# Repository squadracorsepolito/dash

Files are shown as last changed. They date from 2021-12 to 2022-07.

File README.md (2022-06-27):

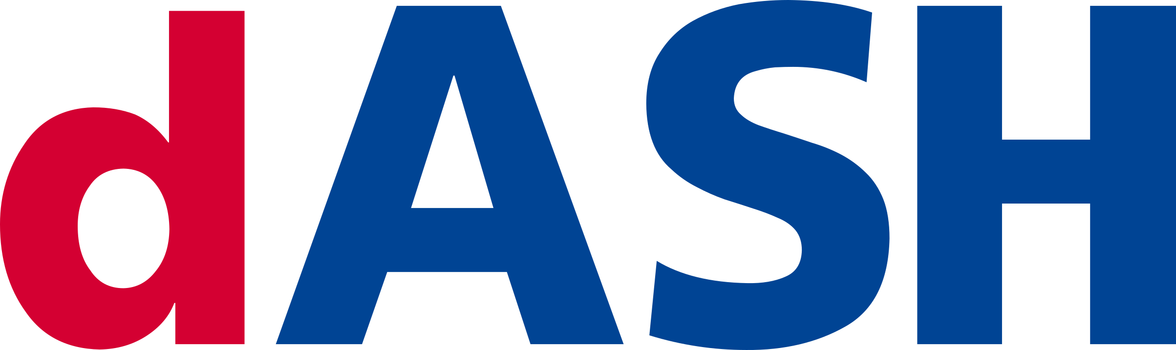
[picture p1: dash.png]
Dash

Benvenuti nella repository ufficiale certificata contenente i file utilizzati per la scheda NuovaDash22© utilizzata dal team Squadra Corse Driverless nell'anno 2021/22

Repository mantenuta da Matteo Bonora (Software) e Francesco Minichelli (Hardware e Software)

## How to use the makefile
This project is generated to work with bare makefiles instead of the STM32CubeIDE. In order to successfully use the makefiles, you need to have a few tools installed. Refer to [this](https://www.bonnee.me/blog/stm32-vscode/) guide on how to setup your environment and install the needed tools (Visual Studio Code is optional and only needed to do debugging and to regenerate the makefile after regenerating code through STM32CubeMX).

If you want to **flash over CAN-bus**, you will need an [additional tool](https://github.com/arkku/srec) to convert the `.bin` firmware file to `.srec` and [bootcommander](https://www.feaser.com/openblt/doku.php?id=manual:bootcommander) to send the firmware to the dashboard.

### Build
In order to build the project, issue the following command:
`make -f STM32Make.make`
You can call `make clean` to clean the build directory.

### Flash
To configure the `can0` interface on your computer, you can call `make can` with root privileges.

`make canflash` will automatically convert the firmware to Motorola S-Record and pass it to bootcommander. If you only want to have the `.srec` file, you can call `make srec`

## Configurazione STM32CubeIDE per upload software tramite CAN

Project Properties -> C/C++ Build -> Settings -> Tool Settings -> MCU Post build outputs -> Selezionare "Convert to Motorola S-record file (-O ihex)"

### Run this command on the terminal to upload the code

1) Setup CAN0 interface with a Kvaser device connected to the PC Host
2a) Open MicroBoot
2b) Open BootCommander (same as MicroBoot but on a terminal)
3) Make sure the Target board is off and the can bus of the board connected to the Kvaser
  - There should be no problem if other device are connected on same can bus. If problem arises, turn off all other devices.
4a) Setup MicroBoot with the firmware to upload. 
4b) Lunch the terminal command
5) Power on the Target board.

```shell
cd /home/francesco/Desktop/openblt-master/Host
sudo ip link set can0 type can bitrate 1000000
sudo ip link set can0 up
./MicroBoot
```

La configurazione attuale è la seguente
CAN SPEED = 1Mbit
CAN message ID target-\>host = (0xFFA)
CAN message ID host-\>target = (0x007)

## Analisi NuovaDash22

I Micro attualmente utilizzati sono:
- STM32F303VCTx (256Kb version)
- STM32F303VETx (512Kb version)

Le periferiche attualmente utilizzate sono:
- CAN
- GPIO

Di seguito una descrizione (tensione, impedenza) per ogni pin del connettore in base all'uscita del micro.

| Signal Name  	| GPIO PIN SET 	 | GPIO PIN RESET | PIN NAME |
| --- | --- | --- | --- |
| ASB CMD  	| ASB LED ON  	 | ASB LED OFF	  | PA8 |
| AMS CMD  	| AMS LED ON  	 | AMS LED OFF | PC6 |
| IMD CMD  	| IMD LED ON  	 | IMD LED OFF | PC8 |
| RTD CMD  	| RTD LED ON  	 | RTD LED OFF | PC6 |
| TSOFF CMD  	| TSOFF LED ON 	 | TSOFF LED OFF  | PC11 |
| ASSI B CMD  	| ASSI B LED OFF | ASSI B LED ON  | PB8 |
| ASSI Y CMD  	| ASSI Y LED OFF | ASSI Y LED ON  | PB7 |
| AMI 1 CMD  	| AMI 1 LED OFF  | AMI 1 LED ON | PB5 |
| AMI 2 CMD  	| AMI 2 LED OFF  | AMI 2 LED ON | PD6 |
| AMI 3 CMD  	| AMI 3 LED OFF  | AMI 3 LED ON | PD4 |

Appena la scheda parte, sia durante il bootloader che durante le prime fasi del programma (1 secondo di bootloader + [0-2.5 max] secondi di programma), al fine di rispettare la regola T11.9.5 che cito: 

> T 11.9.5 Indicators according to T 11.9.1 with safe state “illuminated” (e.g. absence of failures is not actively indicated) must be illuminated for 1 s to 3 s for visible check after power cycling the LVMS. 

ci si aspetta il seguente stato per ogni apparato della macchina:

- LED ASSI YELLOW (durante i test questo colore sarà BLU)
- LED AMI tutti accesi
- BuzzerAS Spento
- BuzzerEv Spento
- Cockpit tutto acceso tranne TSOFF

### Analisi Dashboard SC19

La scheda può essere suddivisa in 4 sezioni:

- MCU (STM32)
- Input/Output (Connettore)
- Alimentazione (DC/DC)
- Condizionamento Output/Input

### MCU (STM32)
Il micro utilizzato è un **STM32F303VCT**. 
- Alimentato con una tensione di 3.3V (ricavata tramite modulo DC/DC sulla scheda)
- Collegamento CAN con transreceiver SN65HVD234
- Connettore SWD
- Tre LED sulla scheda, RED/GREEN/BLUE, collegati rispettivamente ai pin PE11, PE12, PA3 e comandati tramite MOSFET (sulla scheda)
- GPIO (verranno spiegati in seguito)
  - PD10 : Imd\_Err\_Led\_Cmd
  - PE2: Buzzer\_CMD
  - PE3: No\_Hv\_Led\_CMD
  - PE5: Rtd\_Led\_CMD
  - PD13: PWM1
  - PD14: PWM2
  - PD15: PWM3
  - PA1: spare\_button
  - PA2: RTD\_button (RTD\_In)
  - PB9: BMS\_Led\_Cmd
- I2C
- USART
### Input/Output (Connettore)
### Alimentazione (DC/DC)
Input a 24V e output a 5V e 3.3V. Per la 5V è stato utilizzato un LMZ14202TZE e per la 3.3V un LM1117-3.3
### Condizionamento Output/Input
I seguenti segnali, provenienti dal connettore, sono collegati a un MOSFET con Source collegato a massa. Tra parentesi, il nome del GPIO della STM che controlla il mosfet
- IMD\_LED (IMD\_LED\_CMD)
- BMS\_LED (BMS\_LED\_CMD)
- RTD\_LED (RTD\_LED\_CMD)
- BUZZER (BUZZER\_CMD)
- No\_Hv\_Led (No\_Hv\_Led\_CMD)
- PUMP\_AUTO (PWM3)
- BP\_FAN\_AUTO (PWM2)
- RAD\_FAN\_AUTO (PWM1)

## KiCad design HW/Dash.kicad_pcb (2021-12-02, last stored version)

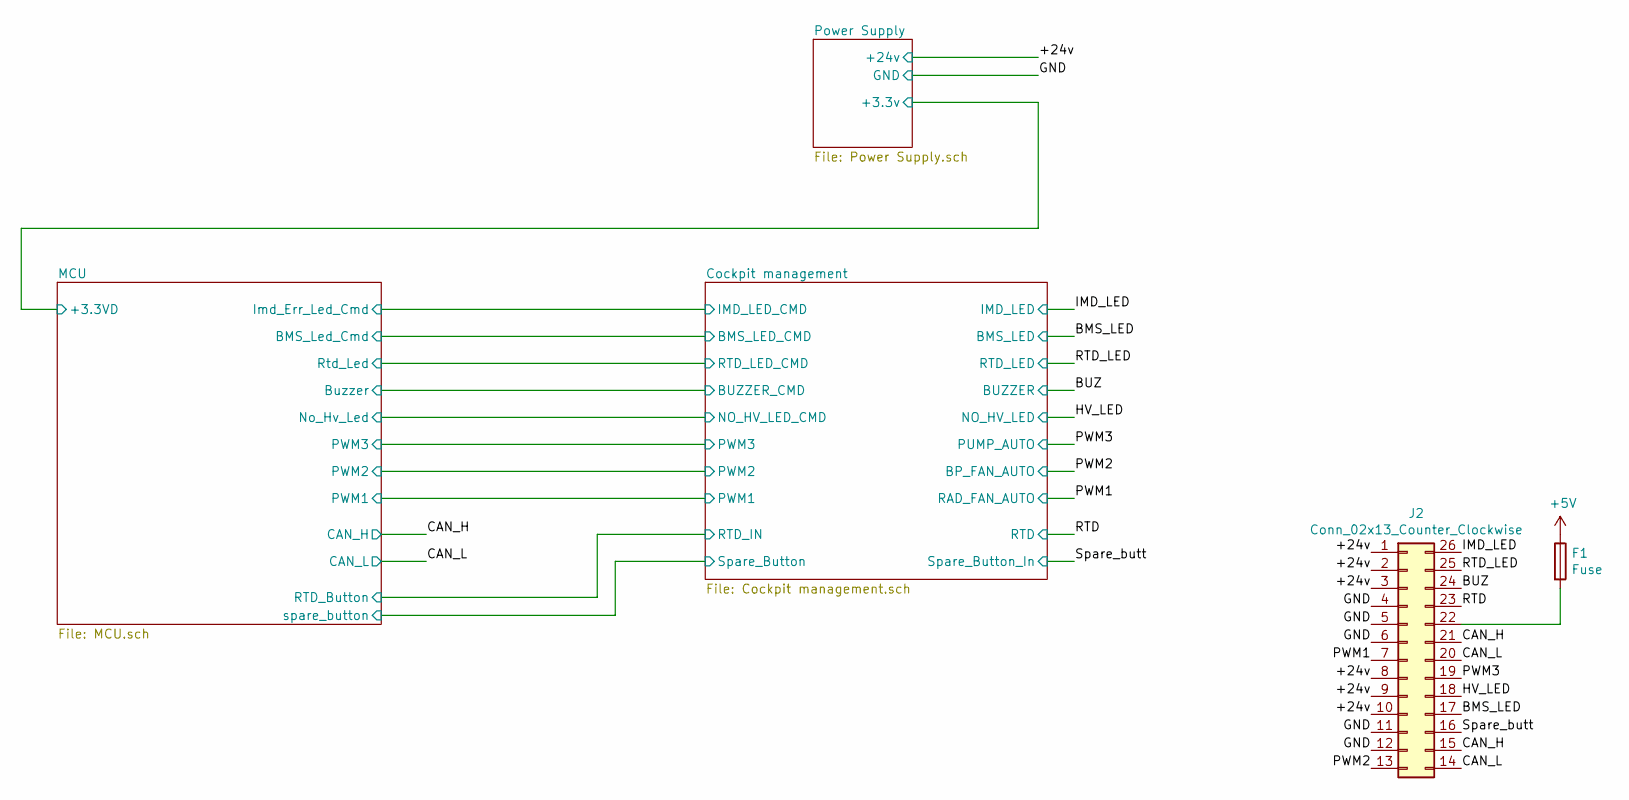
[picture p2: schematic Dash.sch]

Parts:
F1: Fuse; Fuse_0805_2012Metric_Pad1.15x1.40mm_HandSolder
J2: Conn_02x13_Counter_Clockwise; TE_9-6437287-8

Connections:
+5V: F1.1; also elsewhere on the board
/+24v: J2.1, J2.2, J2.3, J2.8, J2.9, J2.10; also elsewhere on the board
/BMS_LED: J2.17; also elsewhere on the board
/BUZ: J2.24; also elsewhere on the board
/CAN_H: J2.15, J2.21; also elsewhere on the board
/CAN_L: J2.14, J2.20; also elsewhere on the board
/HV_LED: J2.18; also elsewhere on the board
/IMD_LED: J2.26; also elsewhere on the board
/PWM1: J2.7; also elsewhere on the board
/PWM2: J2.13; also elsewhere on the board
/PWM3: J2.19; also elsewhere on the board
/RTD: J2.23; also elsewhere on the board
/RTD_LED: J2.25; also elsewhere on the board
/Spare_butt: J2.16; also elsewhere on the board
GND: J2.4, J2.5, J2.6, J2.11, J2.12; also elsewhere on the board
unnamed: F1.2, J2.22

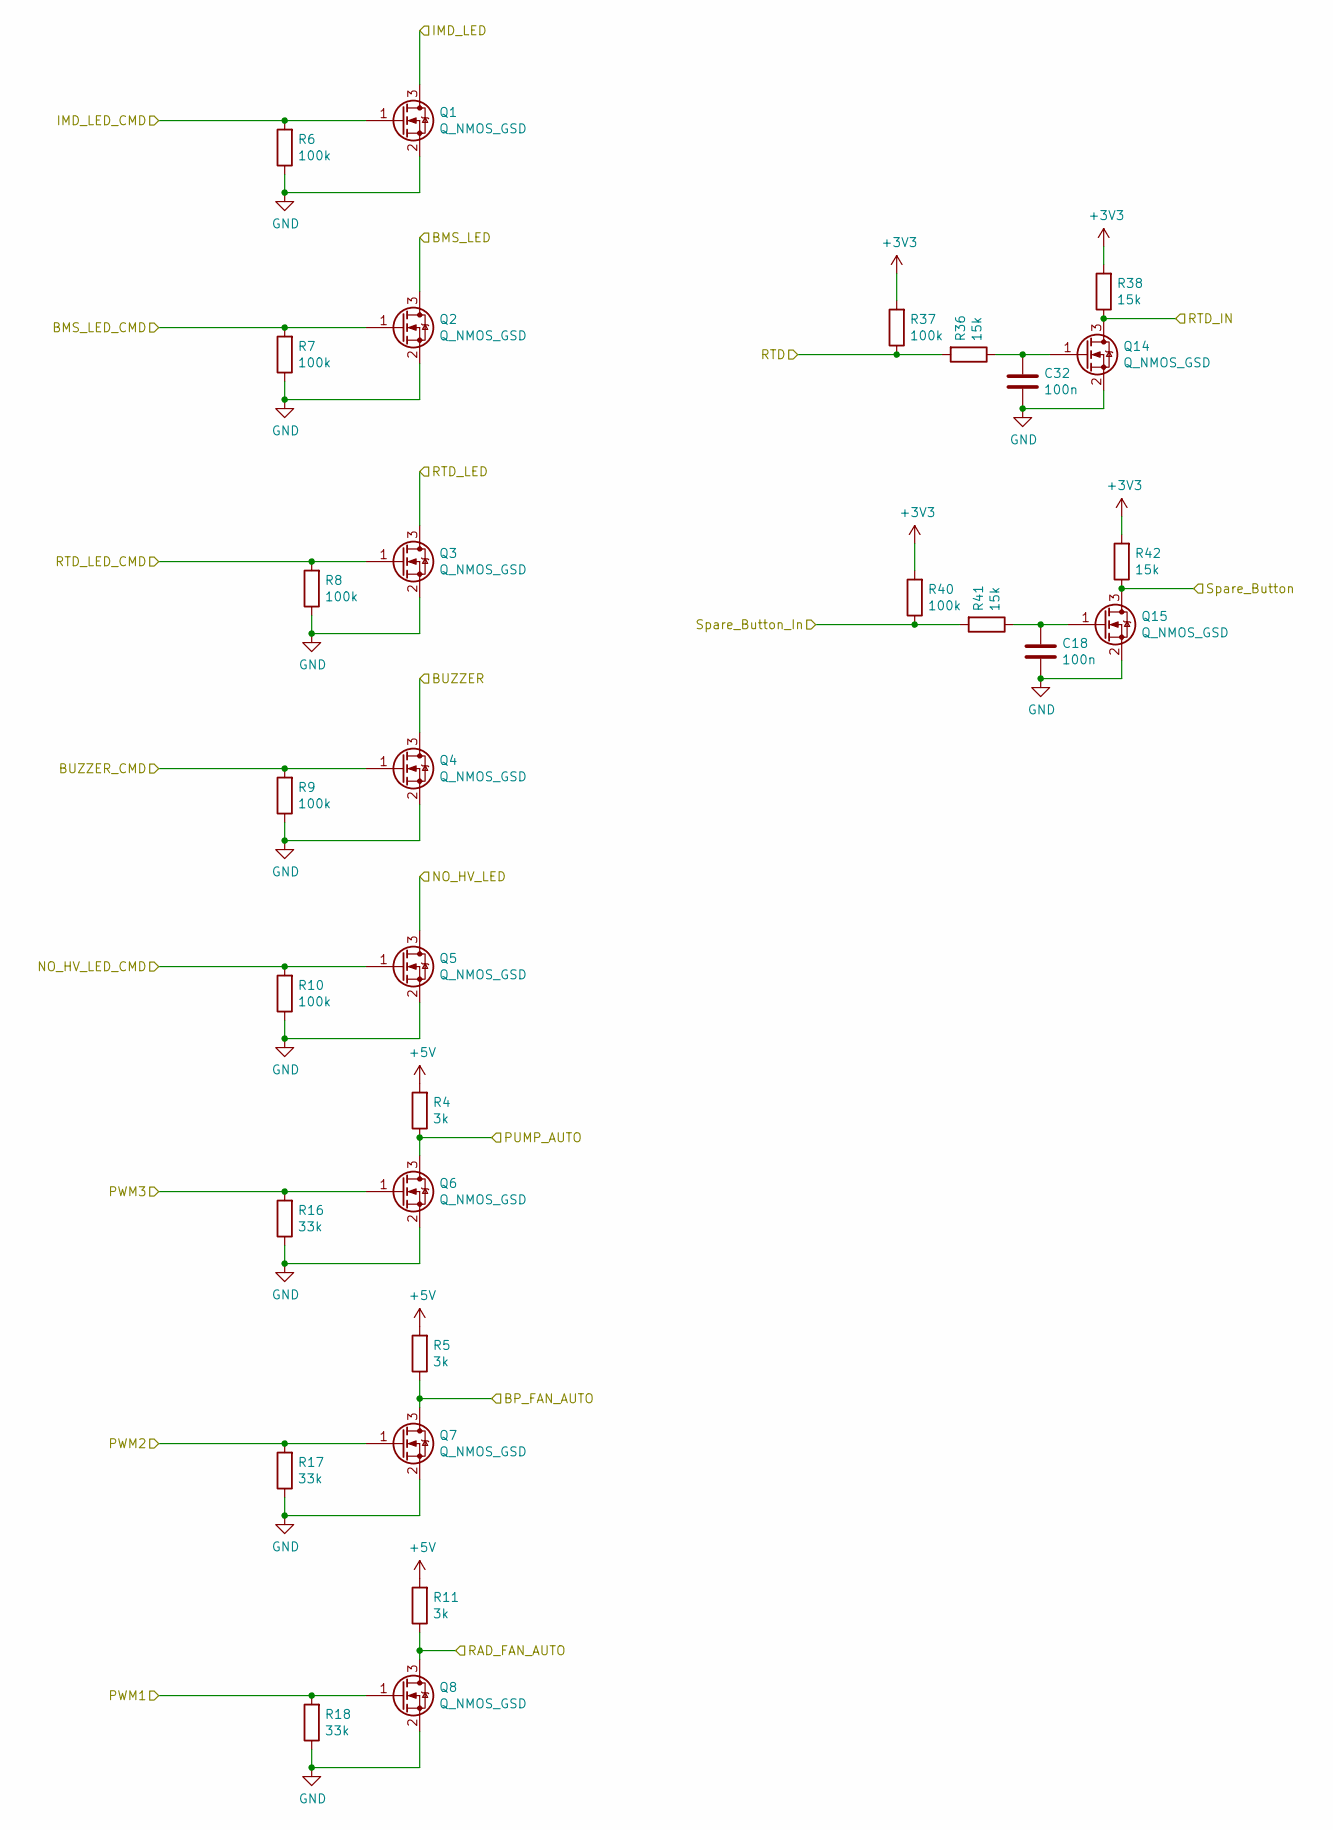
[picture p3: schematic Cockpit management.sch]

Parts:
C18, C32: 100n; C_0805_2012Metric_Pad1.15x1.40mm_HandSolder
Q1, Q2, Q3, Q4, Q5, Q6, Q7, Q8, Q14, Q15: Q_NMOS_GSD; SOT-23
R4, R5, R11: 3k; R_0603_1608Metric_Pad1.05x0.95mm_HandSolder
R6, R7, R8, R9, R10, R37, R40: 100k; R_0603_1608Metric_Pad1.05x0.95mm_HandSolder
R16, R17, R18: 33k; R_0603_1608Metric_Pad1.05x0.95mm_HandSolder
R36, R38, R41, R42: 15k; R_0603_1608Metric_Pad1.05x0.95mm_HandSolder

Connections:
+3V3: R37.2, R38.2, R40.2, R42.2; also elsewhere on the board
+5V: R4.2, R5.2, R11.2; also elsewhere on the board
/BMS_LED: Q2.3 (D); also elsewhere on the board
/BUZ: Q4.3 (D); also elsewhere on the board
/Cockpit management/BMS_LED_CMD: Q2.1 (G), R7.2; also elsewhere on the board
/Cockpit management/BUZZER_CMD: Q4.1 (G), R9.2; also elsewhere on the board
/Cockpit management/IMD_LED_CMD: Q1.1 (G), R6.2; also elsewhere on the board
/Cockpit management/NO_HV_LED_CMD: Q5.1 (G), R10.2; also elsewhere on the board
/Cockpit management/PWM1: Q8.1 (G), R18.2; also elsewhere on the board
/Cockpit management/PWM2: Q7.1 (G), R17.2; also elsewhere on the board
/Cockpit management/PWM3: Q6.1 (G), R16.2; also elsewhere on the board
/Cockpit management/RTD_LED_CMD: Q3.1 (G), R8.2; also elsewhere on the board
/Cockpit management/Spare_Button: Q15.3 (D), R42.1; also elsewhere on the board
/HV_LED: Q5.3 (D); also elsewhere on the board
/IMD_LED: Q1.3 (D); also elsewhere on the board
/MCU/RTD_Button: Q14.3 (D), R38.1; also elsewhere on the board
/PWM1: Q8.3 (D), R11.1; also elsewhere on the board
/PWM2: Q7.3 (D), R5.1; also elsewhere on the board
/PWM3: Q6.3 (D), R4.1; also elsewhere on the board
/RTD: R36.2, R37.1; also elsewhere on the board
/RTD_LED: Q3.3 (D); also elsewhere on the board
/Spare_butt: R40.1, R41.2; also elsewhere on the board
GND: C18.2, C32.2, Q1.2 (S), Q2.2 (S), Q3.2 (S), Q4.2 (S), Q5.2 (S), Q6.2 (S), Q7.2 (S), Q8.2 (S), Q14.2 (S), Q15.2 (S), R6.1, R7.1, R8.1, R9.1, R10.1, R16.1, R17.1, R18.1; also elsewhere on the board
unnamed: C18.1, Q15.1 (G), R41.1
unnamed: C32.1, Q14.1 (G), R36.1

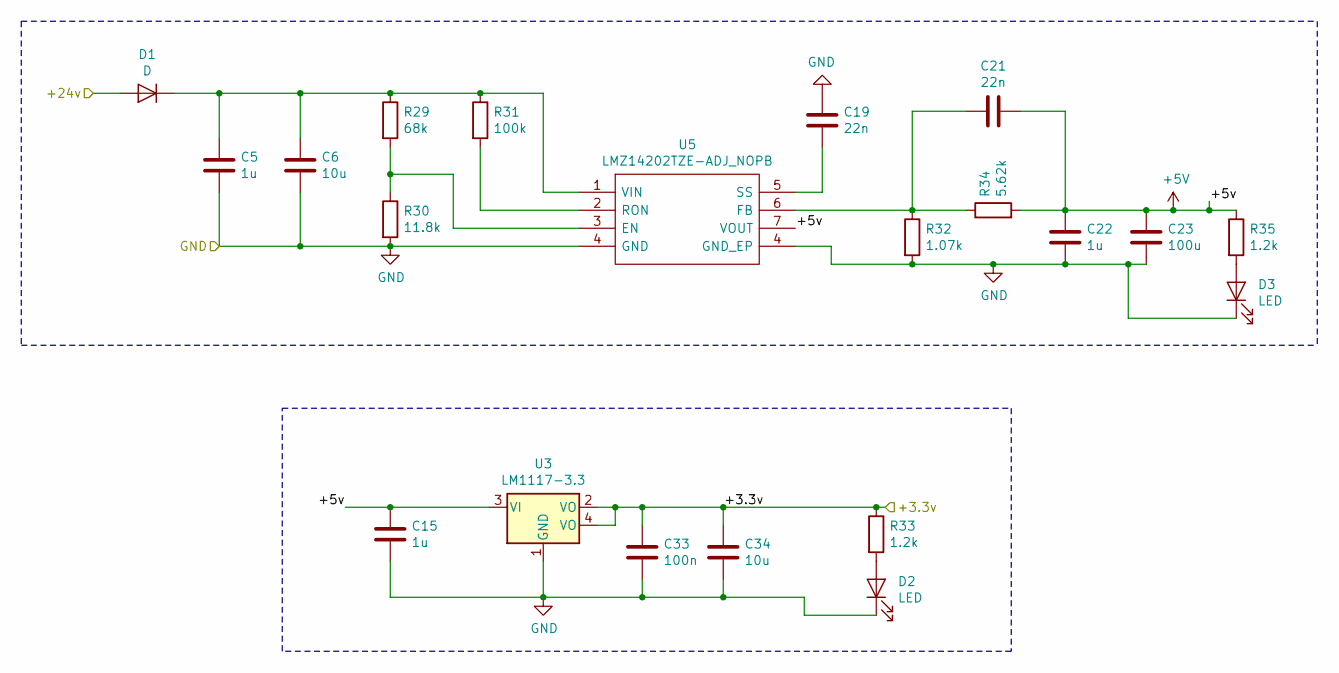
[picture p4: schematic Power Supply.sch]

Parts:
C5, C15, C22: 1u; C_0805_2012Metric_Pad1.15x1.40mm_HandSolder
C6, C34: 10u; C_1206_3216Metric_Pad1.42x1.75mm_HandSolder
C19, C21: 22n; C_0805_2012Metric_Pad1.15x1.40mm_HandSolder
C23: 100u; C_1206_3216Metric_Pad1.42x1.75mm_HandSolder
C33: 100n; C_0805_2012Metric_Pad1.15x1.40mm_HandSolder
D1: D; D_SOD-123
D2, D3: LED; LED_0805_2012Metric_Pad1.15x1.40mm_HandSolder
R29: 68k; R_0603_1608Metric_Pad1.05x0.95mm_HandSolder
R30: 11.8k; R_0603_1608Metric_Pad1.05x0.95mm_HandSolder
R31: 100k; R_0603_1608Metric_Pad1.05x0.95mm_HandSolder
R32: 1.07k; R_0603_1608Metric_Pad1.05x0.95mm_HandSolder
R33, R35: 1.2k; R_0603_1608Metric_Pad1.05x0.95mm_HandSolder
R34: 5.62k; R_0603_1608Metric_Pad1.05x0.95mm_HandSolder
U3: LM1117-3.3; SOT-223; Manufacturer_Part_Number LM1117MP-3.3/NOPB
U5: LMZ14202TZE-ADJ_NOPB; TO-PMOD-7; Manufacturer_Part_Number LMZ14202TZE-ADJ/NOPB

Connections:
+3V3: C33.1, C34.1, R33.1, U3.2 (VO), U3.4 (VO); also elsewhere on the board
+5V: C15.1, C21.1, C22.1, C23.1, R34.2, R35.1, U3.3 (VI), U5.7 (VOUT); also elsewhere on the board
/+24v: D1.2 (A); also elsewhere on the board
GND: C5.2, C6.2, C15.2, C19.1, C22.2, C23.2, C33.2, C34.2, D2.1 (K), D3.1 (K), R30.2, R32.2, U3.1 (GND), U5.4 (GND); also elsewhere on the board
unnamed: C5.1, C6.1, D1.1 (K), R29.1, R31.1, U5.1 (VIN)
unnamed: C19.2, U5.5 (SS)
unnamed: C21.2, R32.1, R34.1, U5.6 (FB)
unnamed: D2.2 (A), R33.2
unnamed: D3.2 (A), R35.2
unnamed: R29.2, R30.1, U5.3 (EN)
unnamed: R31.2, U5.2 (RON)

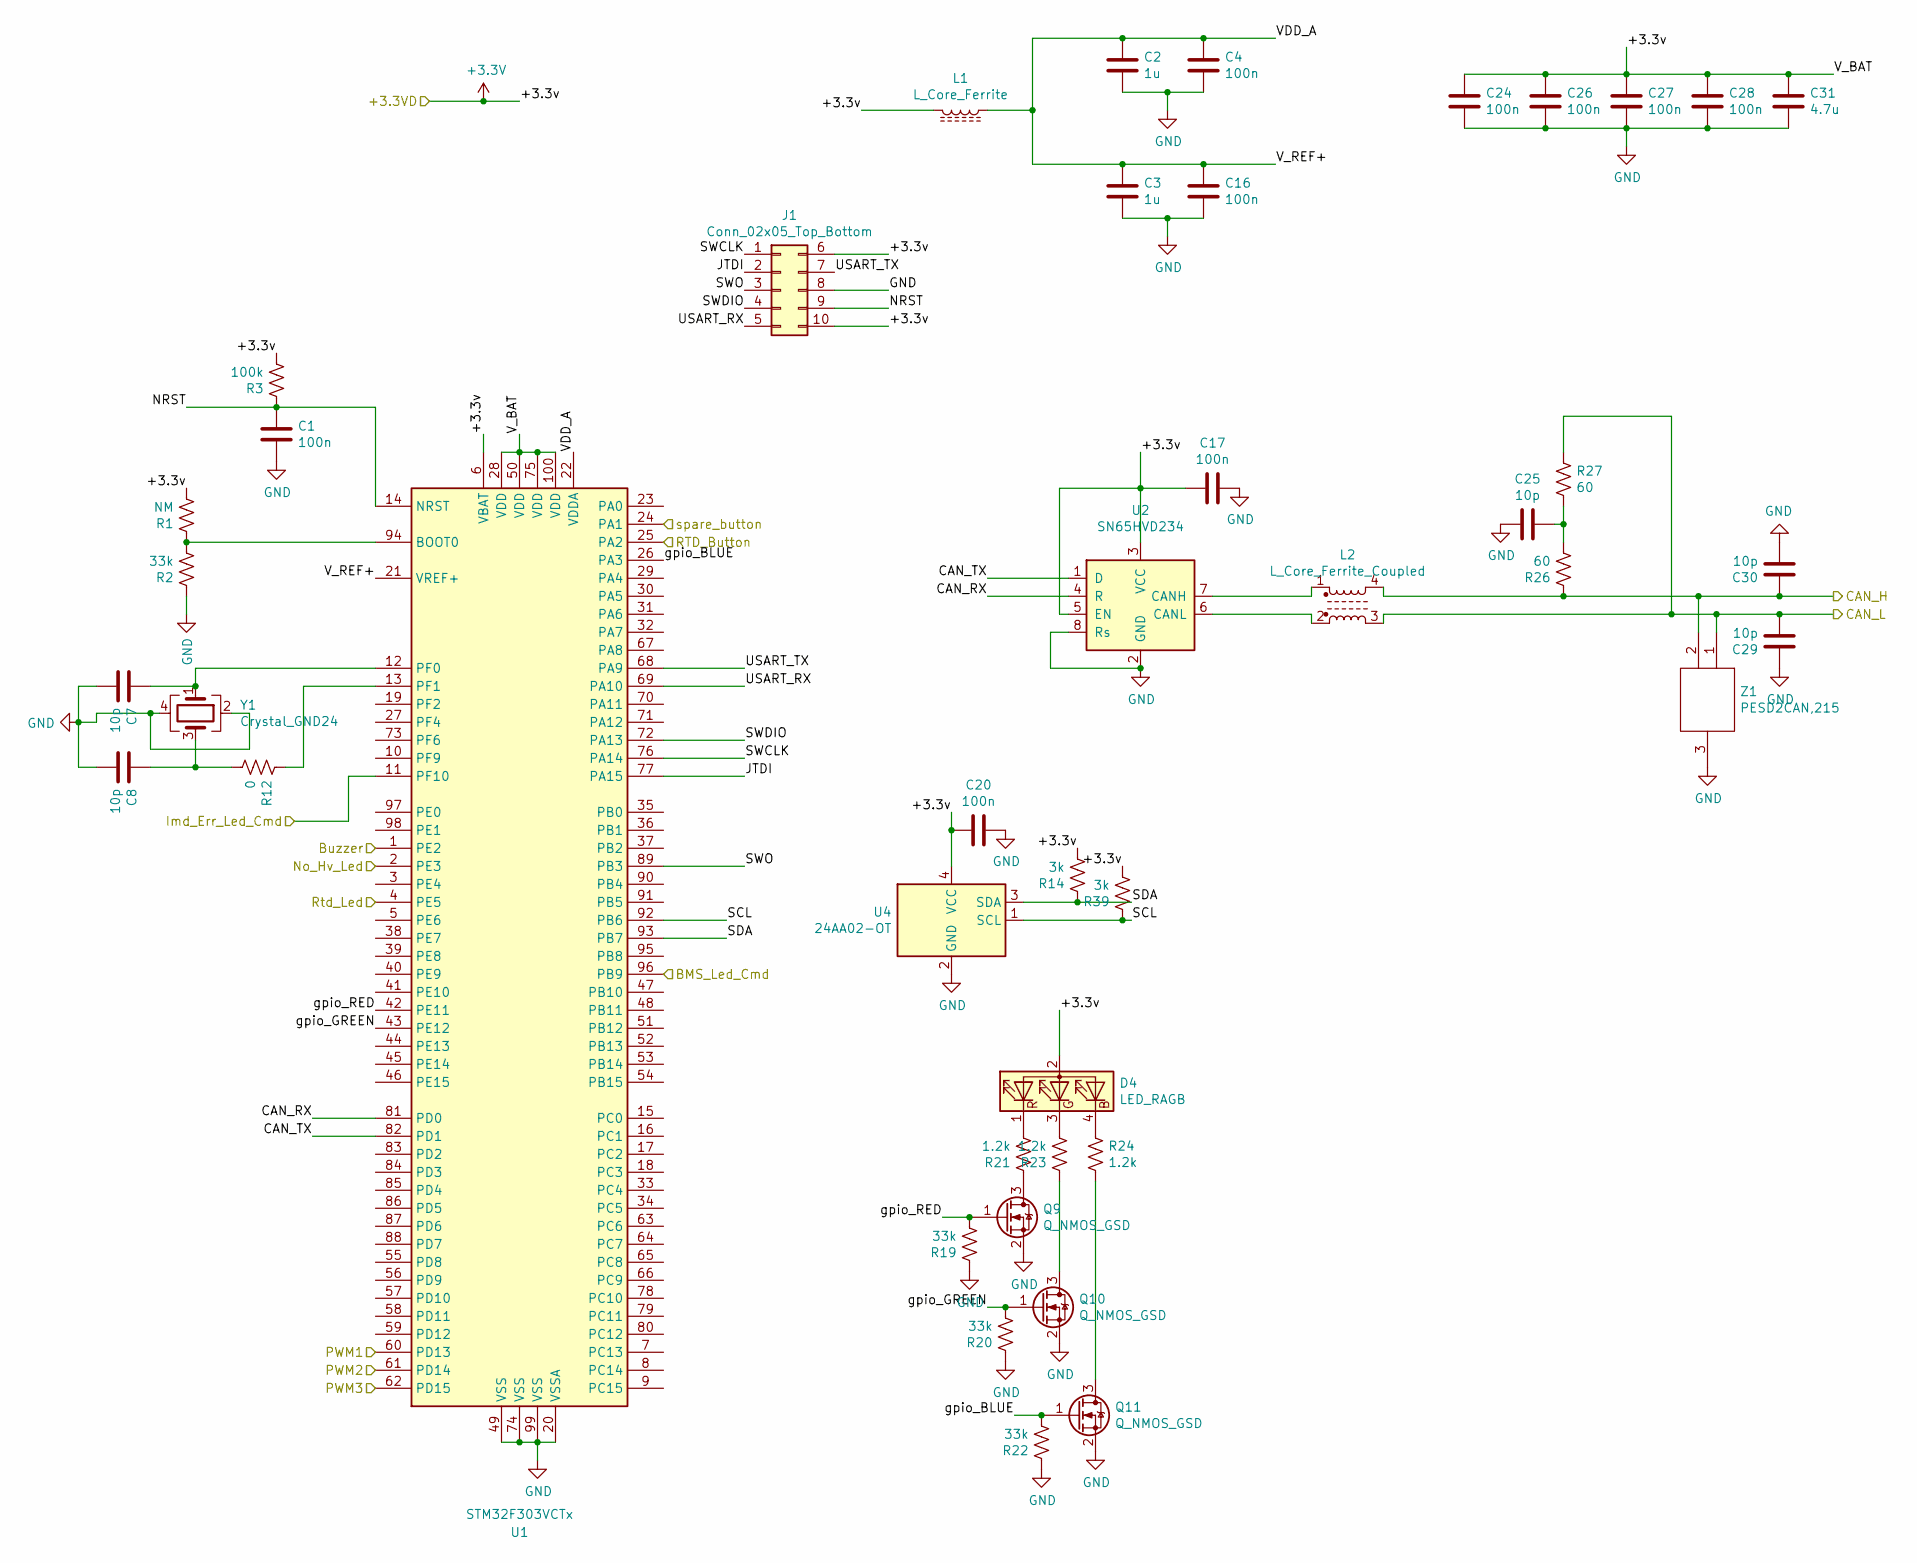
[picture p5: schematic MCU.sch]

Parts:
C1, C4, C16, C17, C20, C24, C26, C27, C28: 100n; C_0805_2012Metric_Pad1.15x1.40mm_HandSolder
C2, C3: 1u; C_0805_2012Metric_Pad1.15x1.40mm_HandSolder
C7, C8: 10p; C_0603_1608Metric_Pad1.05x0.95mm_HandSolder
C25, C29, C30: 10p; C_0805_2012Metric_Pad1.15x1.40mm_HandSolder
C31: 4.7u; C_0805_2012Metric_Pad1.15x1.40mm_HandSolder
D4: LED_RAGB; Kingbright PLCC4
J1: Conn_02x05_Top_Bottom; Pin_Header_Straight_2x05_Pitch2.00mm
L1: L_Core_Ferrite; L_0603_1608Metric_Pad1.05x0.95mm_HandSolder; Manufacturer_Part_Number BKP1608HS600-T
L2: L_Core_Ferrite_Coupled; ACT45B
Q9, Q10, Q11: Q_NMOS_GSD; SOT-23
R1: NM; R_0603_1608Metric_Pad1.05x0.95mm_HandSolder
R2, R19, R20, R22: 33k; R_0603_1608Metric_Pad1.05x0.95mm_HandSolder
R3: 100k; R_0603_1608Metric_Pad1.05x0.95mm_HandSolder
R12: 0; R_0603_1608Metric_Pad1.05x0.95mm_HandSolder
R14, R39: 3k; R_0603_1608Metric_Pad1.05x0.95mm_HandSolder
R21, R23, R24: 1.2k; R_0603_1608Metric_Pad1.05x0.95mm_HandSolder
R26, R27: 60; R_0603_1608Metric_Pad1.05x0.95mm_HandSolder
U1: STM32F303VCTx; LQFP-100_14x14mm_P0.5mm; Manufacturer_Part_Number STM32F303VCT6
U2: SN65HVD234; SOIC-8_3.9x4.9mm_P1.27mm; Manufacturer_Part_Number SN65HVD234DR
U4: 24AA02-OT; SOT-23-5_HandSoldering
Y1: Crystal_GND24; Crystal_SMD_Abracon_ABM3B-4Pin_5.0x3.2mm
Z1: PESD2CAN,215; SOT-23; Mouser Part Number 771-PESD2CAN-T/R

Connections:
+3V3: C17.2, C20.2, C24.1, C26.1, C27.1, C28.1, C31.1, D4.2 (A), J1.6, J1.10, L1.2, R1.2, R3.2, R14.2, R39.2, U1.6 (VBAT), U1.28 (VDD), U1.50 (VDD), U1.75 (VDD), U1.100 (VDD), U2.3 (VCC), U2.5 (EN), U4.4 (VCC); also elsewhere on the board
/CAN_H: C30.2, L2.4, R26.1, Z1.2; also elsewhere on the board
/CAN_L: C29.1, L2.3, R27.1, Z1.1; also elsewhere on the board
/Cockpit management/BMS_LED_CMD: U1.96 (PB9); also elsewhere on the board
/Cockpit management/BUZZER_CMD: U1.1 (PE2); also elsewhere on the board
/Cockpit management/IMD_LED_CMD: U1.11 (PF10); also elsewhere on the board
/Cockpit management/NO_HV_LED_CMD: U1.2 (PE3); also elsewhere on the board
/Cockpit management/PWM1: U1.60 (PD13); also elsewhere on the board
/Cockpit management/PWM2: U1.61 (PD14); also elsewhere on the board
/Cockpit management/PWM3: U1.62 (PD15); also elsewhere on the board
/Cockpit management/RTD_LED_CMD: U1.4 (PE5); also elsewhere on the board
/Cockpit management/Spare_Button: U1.24 (PA1); also elsewhere on the board
/MCU/CAN_RX: U1.81 (PD0), U2.4 (R)
/MCU/CAN_TX: U1.82 (PD1), U2.1 (D)
/MCU/JTDI: J1.2, U1.77 (PA15)
/MCU/NRST: C1.1, J1.9, R3.1, U1.14 (NRST)
/MCU/RTD_Button: U1.25 (PA2); also elsewhere on the board
/MCU/SCL: R39.1, U1.92 (PB6), U4.1 (SCL)
/MCU/SDA: R14.1, U1.93 (PB7), U4.3 (SDA)
/MCU/SWCLK: J1.1, U1.76 (PA14)
/MCU/SWDIO: J1.4, U1.72 (PA13)
/MCU/SWO: J1.3, U1.89 (PB3)
/MCU/USART_RX: J1.5, U1.69 (PA10)
/MCU/USART_TX: J1.7, U1.68 (PA9)
/MCU/VDD_A: C2.1, C3.1, C4.1, C16.1, L1.1, U1.21 (VREF+), U1.22 (VDDA)
/MCU/gpio_BLUE: Q11.1 (G), R22.2, U1.26 (PA3)
/MCU/gpio_GREEN: Q10.1 (G), R20.2, U1.43 (PE12)
/MCU/gpio_RED: Q9.1 (G), R19.2, U1.42 (PE11)
GND: C1.2, C2.2, C3.2, C4.2, C7.2, C8.2, C16.2, C17.1, C20.1, C24.2, C25.2, C26.2, C27.2, C28.2, C29.2, C30.1, C31.2, J1.8, Q9.2 (S), Q10.2 (S), Q11.2 (S), R2.1, R19.1, R20.1, R22.1, U1.20 (VSSA), U1.49 (VSS), U1.74 (VSS), U1.99 (VSS), U2.2 (GND), U2.8 (Rs), U4.2 (GND), Y1.2, Y1.4, Z1.3; also elsewhere on the board
unnamed: C7.1, U1.12 (PF0), Y1.1
unnamed: C8.1, R12.2, Y1.3
unnamed: C25.1, R26.2, R27.2
unnamed: D4.1 (RK), R21.2
unnamed: D4.3 (GK), R23.2
unnamed: D4.4 (BK), R24.1
unnamed: L2.1, U2.7 (CANH)
unnamed: L2.2, U2.6 (CANL)
unnamed: Q9.3 (D), R21.1
unnamed: Q10.3 (D), R23.1
unnamed: Q11.3 (D), R24.2
unnamed: R1.1, R2.2, U1.94 (BOOT0)
unnamed: R12.1, U1.13 (PF1)

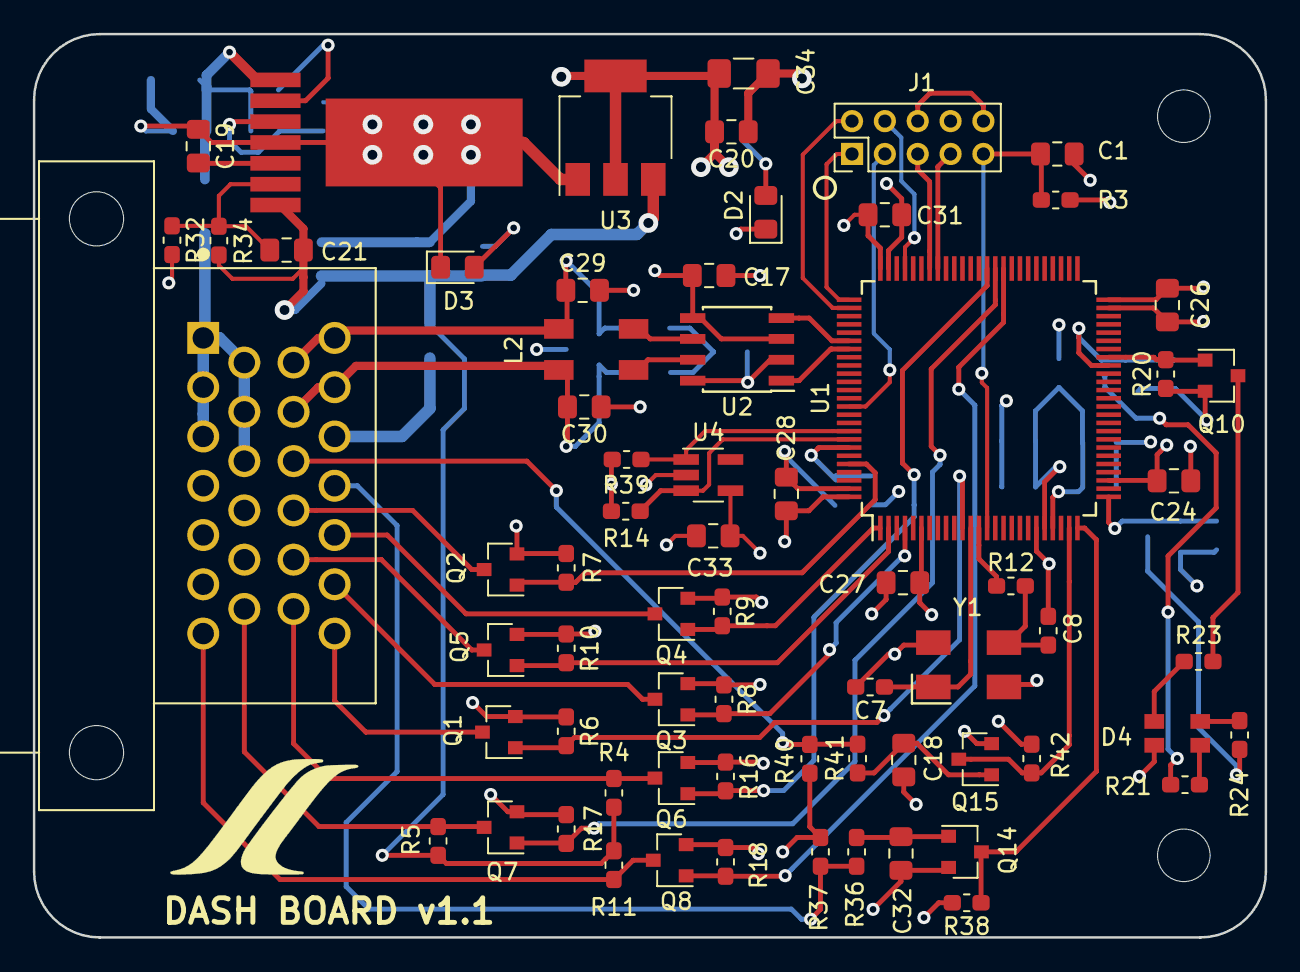
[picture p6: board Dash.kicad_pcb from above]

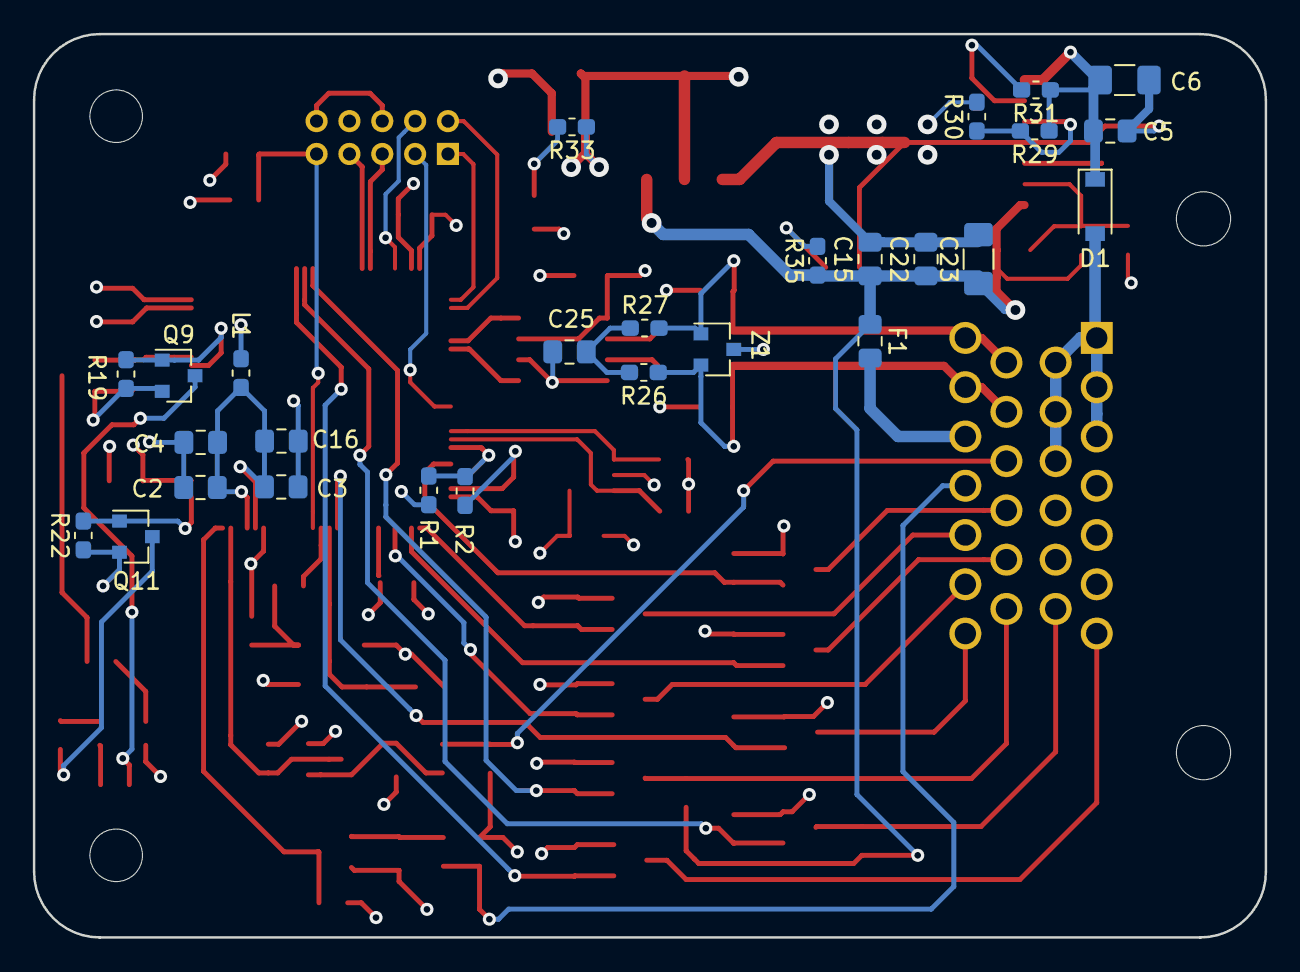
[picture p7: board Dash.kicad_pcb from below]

Board: 4 copper layers, 75.0 x 55.0 mm, 95 parts (27 on the bottom side), 64 nets.

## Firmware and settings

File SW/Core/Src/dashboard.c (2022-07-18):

/*INCLUDE*/

#include "dashboard.h"
#include "as_fsm.h"
#include "button.h"
#include "can.h"
#include "mission.h"
#include "tim.h"
#include "usart.h"
#include "utils.h"
#include "wdg.h"
#include <stdio.h>

/* Dashboard State Machine */
typedef enum
{
    STATE_IDLE = 0,
    STATE_CTOR_EN_WAIT_ACK,
    STATE_TS_ON,
    STATE_RTD_WAIT_ACK,
    STATE_RTD,
    STATE_IDLE_WAIT_ACK,
    STATE_ERROR
} state;

/* State change triggers */
typedef enum
{
    TRIG_NONE = 0, // No trigger/triggered by CAN bus
    TRIG_COCK = 1, // Cockpit button
    TRIG_EXT = 2   // External button
} state_trig;
state_trig STATE_CHANGE_TRIG = TRIG_NONE;

// FSM state keeping
state rtd_fsm = STATE_IDLE;

CAN_TxHeaderTypeDef TxHeader;
CAN_RxHeaderTypeDef RxHeader;
uint32_t TxMailbox;
uint8_t TxData[8] = {0};
uint8_t RxData[8] = {0};

/* Error Variables */
error_t error = ERROR_NONE;
uint8_t boards_timeouts;

/* Cock LEDs flags */
volatile bool ASB_ERR;
volatile bool BMS_ERR;
volatile bool TSOFF;
volatile bool IMD_ERR;

/* dSpace ACK flags */
volatile bool CTOR_EN_ACK;
volatile bool RTD_EN_ACK;
volatile bool IDLE_ACK;
volatile bool NACK;

/* PWM Variables */
volatile uint8_t PWM_POWERTRAIN;
volatile uint8_t PWM_BAT_FAN;
volatile uint16_t PWM_ASB_MOTOR;

/* Button short press flags */
bool COCK_BUTTON = false;
bool EXT_BUTTON = false;

/*CUSTOM FUNCTIONS*/

/*Rx Message interrupt from CAN*/
void HAL_CAN_RxFifo0MsgPendingCallback(CAN_HandleTypeDef *hcan)
{
    if (HAL_CAN_GetRxMessage(hcan, CAN_RX_FIFO0, &RxHeader, RxData) != HAL_OK)
    {
        /* Transmission request Error */
        HAL_CAN_ResetError(hcan);
        Error_Handler();
    }

    // Reset watchdog
    uint32_t now = ReturnTime_100us();
    switch (RxHeader.StdId)
    {
    case EBS_CMD_ID_CAN:
    case ASB_CMD_ID_CAN:
    case AS_STATE_ID_CAN:
    case FSM_ACK_ID_CAN:
    case PWM_CMD_ID_CAN:
        // Reset dSpace timeout after boot
        wdg_timeouts_100us[WDG_BOARD_DSPACE] = 5000;
        wdg_reset(WDG_BOARD_DSPACE, now);
        break;
    case TLB_ERROR_ID_CAN:
        wdg_reset(WDG_BOARD_TLB, now);
        break;
    }

    /*Reboot Board - Received command byte from CAN*/
    if ((RxHeader.StdId == BOOTLOADER_ID_CAN) && (RxHeader.DLC == 2) && (RxData[0] == 0xFF) && (RxData[1] == 0x00))
    {
        NVIC_SystemReset();
    }

    /*
     *
     * dSpace
     *
     */
    /*EBS commmand*/
    else if ((RxHeader.StdId == EBS_CMD_ID_CAN) && (RxHeader.DLC == 1))
    {
        HAL_GPIO_WritePin(EBS_RELAY1_GPIO_Port, EBS_RELAY1_Pin, RxData[0] & 0b1);
        HAL_GPIO_WritePin(EBS_RELAY2_GPIO_Port, EBS_RELAY2_Pin, (RxData[0] >> 1) & 0b1);
    }
    /* ASB command */
    else if ((RxHeader.StdId == ASB_CMD_ID_CAN) && (RxHeader.DLC == 1))
    {
        // Min PWM pulse=800 (800us)
        // Max PWM pulse=2100 (2.1ms)
        PWM_ASB_MOTOR = RxData[0] * ((2100 - 800) / 255) + 800;
        __HAL_TIM_SET_COMPARE(&ASB_MOTOR_PWM_TIM, ASB_MOTOR_PWM_CH, PWM_ASB_MOTOR);
    }
    /* AS state */
    else if ((RxHeader.StdId == AS_STATE_ID_CAN) && (RxHeader.DLC == 2))
    {
        ASB_ERR = (bool)(RxData[0] & (1 << 7));
        if (RxData[1] < AS_TEST)
        {
            as_state = RxData[1];
        }
    }
    /* ACK from dSpace */
    else if ((RxHeader.StdId == FSM_ACK_ID_CAN) && (RxHeader.DLC == 1))
    {
        switch (RxData[0])
        {
        case 1:
            CTOR_EN_ACK = true;
            break;
        case 2:
            RTD_EN_ACK = true;
            break;
        case 3:
            IDLE_ACK = true;
            break;
        case 4:
            NACK = true;
            break;
        }
    }
    /* Cooling Command */
    else if ((RxHeader.StdId == PWM_CMD_ID_CAN) && (RxHeader.DLC == 2))
    {
        // Radiator fan and pump signals have been merged to make space for ASB signal.
        PWM_POWERTRAIN = RxData[0];
        __HAL_TIM_SET_COMPARE(&POWERTRAIN_COOLING_PWM_TIM, POWERTRAIN_COOLING_PWM_CH, PWM_POWERTRAIN);

        PWM_BAT_FAN = RxData[1];
        __HAL_TIM_SET_COMPARE(&BAT_FAN_PWM_TIM, BAT_FAN_PWM_CH, PWM_BAT_FAN);
    }

    /*
     *
     * TLB
     *
     */
    /* Received TLB error byte in order to turn LEDs on or off */
    else if ((RxHeader.StdId == TLB_ERROR_ID_CAN) && (RxHeader.DLC == 1) && (RxData[0] < 16))
    {
        TSOFF = (bool)(RxData[0] & 1);
        BMS_ERR = (bool)(RxData[0] & 4) || (bool)(RxData[0] & 2);
        IMD_ERR = (bool)(RxData[0] & 4);
    }
}
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

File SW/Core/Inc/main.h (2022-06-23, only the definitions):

#define EBS_RELAY1_Pin GPIO_PIN_10
#define EBS_RELAY1_GPIO_Port GPIOD
#define EBS_RELAY2_Pin GPIO_PIN_11
#define EBS_RELAY2_GPIO_Port GPIOD
#define COCK_BTN_Pin GPIO_PIN_12
#define COCK_BTN_GPIO_Port GPIOD
#define MISSION_BTN_Pin GPIO_PIN_13
#define MISSION_BTN_GPIO_Port GPIOD
#define BUZZERAS_CMD_Pin GPIO_PIN_14
#define BUZZERAS_CMD_GPIO_Port GPIOD
#define RTD_CMD_Pin GPIO_PIN_6
#define RTD_CMD_GPIO_Port GPIOC
#define BUZZEREV_CMD_Pin GPIO_PIN_7
#define BUZZEREV_CMD_GPIO_Port GPIOC
#define AMS_CMD_Pin GPIO_PIN_8
#define AMS_CMD_GPIO_Port GPIOC
#define EXT_BTN_Pin GPIO_PIN_9
#define EXT_BTN_GPIO_Port GPIOC
#define IMD_CMD_Pin GPIO_PIN_8
#define IMD_CMD_GPIO_Port GPIOA
#define AMI_OFF_CMD_Pin GPIO_PIN_10
#define AMI_OFF_CMD_GPIO_Port GPIOA
#define ASB_SERVO_PWM_CMD_Pin GPIO_PIN_10
#define ASB_SERVO_PWM_CMD_GPIO_Port GPIOC
#define TSOFF_CMD_Pin GPIO_PIN_11
#define TSOFF_CMD_GPIO_Port GPIOC
#define ASB_CMD_Pin GPIO_PIN_12
#define ASB_CMD_GPIO_Port GPIOC
#define LED1_Pin GPIO_PIN_2
#define LED1_GPIO_Port GPIOD
#define LED2_Pin GPIO_PIN_3
#define LED2_GPIO_Port GPIOD
#define AMI3_CMD_Pin GPIO_PIN_4
#define AMI3_CMD_GPIO_Port GPIOD
#define AMI2_CMD_Pin GPIO_PIN_6
#define AMI2_CMD_GPIO_Port GPIOD
#define AMI1_CMD_Pin GPIO_PIN_5
#define AMI1_CMD_GPIO_Port GPIOB
#define ASSI_YELLOW_CMD_Pin GPIO_PIN_7
#define ASSI_YELLOW_CMD_GPIO_Port GPIOB
#define ASSI_BLUE_CMD_Pin GPIO_PIN_8
#define ASSI_BLUE_CMD_GPIO_Port GPIOB
#define BAT_FAN_PWM_CMD_Pin GPIO_PIN_0
#define BAT_FAN_PWM_CMD_GPIO_Port GPIOE
#define POWERTRAIN_COOLING_PWM_CMD_Pin GPIO_PIN_1
#define POWERTRAIN_COOLING_PWM_CMD_GPIO_Port GPIOE
#define BAT_FAN_PWM_TIM htim16
#define BAT_FAN_PWM_CH TIM_CHANNEL_1
#define POWERTRAIN_COOLING_PWM_TIM htim17
#define POWERTRAIN_COOLING_PWM_CH TIM_CHANNEL_1
#define ASB_MOTOR_PWM_TIM htim8
#define ASB_MOTOR_PWM_CH TIM_CHANNEL_1
#define COUNTER_TIM htim3

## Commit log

2021-12-01 First commit - v 1.0
    First commit
    [CAN.sch, Cockpit management.sch, Dash.kicad_pcb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]
2021-12-02 Version 1.1
    Version 1.1
    Hw and Sw improvements
    [Cockpit management.sch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]
2022-04-30 Add button debouncing functions
2022-05-04 Check both RTD buttons and wire up ERROR state. Partially fixes #4
    [button.c, button.h, dashboard.c]
2022-05-08 Add AMI LED support. Adds ami.c/.h files that handle the mission LEDs as described by #9
2022-05-26 Add AS FSM Fixes #8
    [as_fsm.c, button.c, dashboard.c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]
2022-05-30 Wire up CAN message for AS state. Fixes #8
    [dashboard.c]
2022-05-31 Deleted HW, openBLT folder. Added new openBLT
    The HW files and openBLT were out of date. Added the new openBLT
    [CAN.sch, Cockpit management.sch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]
2022-06-06 Add EBS relay command via CAN
2022-06-07 Fix button_get(), remove ASMS stuff
    [button.c, dashboard.c]
2022-06-12 Small fixes to button and mission
    [Dash22.ioc, button.c, button.h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]
2022-06-13 Configure timers for cooling and ASB
2022-06-15 Setup ASB timer and CAN message
2022-06-24 ( ͡° ͜ʖ ͡°)
2022-06-24 Add tentative flow chart
2022-06-24 Follow the flow chart
2022-06-24 Reset all flags after each FSM cycle. Closes #15
    [dashboard.c]
2022-06-24 Fix minor bug on button.c and decouple logical and physical states
    [button.c, button.h, mission.c]
2022-06-27 Add local drivers to avoid absolute paths in makefile
    [Dash22.ioc, can.c, dashboard.c]
2022-06-30 Fix PWM signals for cooling and ASB
    [Dash22.ioc, dashboard.c]
2022-07-07 Add rtd beep. Ma tanto la dspace non mi manda gli ack ¯\_(ツ)_/¯
2022-07-10 Remove useless mission. Enable RTD sound with AS buzzer
    [as_fsm.c, dashboard.c, mission.c]
2022-07-11 Fix conflicts when different systems share the same buzzer
    [as_fsm.c, dashboard.c]

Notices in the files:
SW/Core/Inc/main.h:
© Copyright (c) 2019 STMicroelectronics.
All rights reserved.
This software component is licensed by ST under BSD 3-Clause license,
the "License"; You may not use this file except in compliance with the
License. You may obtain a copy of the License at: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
